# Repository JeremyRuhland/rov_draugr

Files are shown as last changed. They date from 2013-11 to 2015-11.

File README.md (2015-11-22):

Western Washington University Marine Technology Club 2014 ROV: Draugr
=====================================================================

More information can be found on my [WWU MTC page](http://goopypanther.org/seniorProjectWebsite/wwu-marine-technology-club.html) or the [main blog post](http://blog.goopypanther.org/posts/ROV_Project:_Draugr/) about Draugr.

The stuff here's pretty old and probably doesn't reflect the current state of the ROV. Some firmware tweaks may have been made last minute in responce to hardware changes. Only the basic functionality was fully implemented and tested.

You can control the ROV via a screen session and the keyboard, the actual GUI that uses the xbox controller was written by Sean and got stored elsewhere (somewhere?).

File hierarchy
--------------

 * firmware
  * C source files
 * hardware
  * Schematics and gerbers for main control board
 * protocol_documentation
  * Command protocol for designing control software

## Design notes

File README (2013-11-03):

5x h bridges
    4 input         =   20 input
                        3x 8-bit shift registers w/ spi interface
                                5 gpio: miso, mosi, sck, latch, cs
    1 output        =   5 outputs
    1 analog        =   5 analog
        
spi arm interface   =   spi interface
                        4 gpio: miso, mosi, sck, cs

conductivity sensor =   1 analog

temp sensing        =   4 analog

range finder        =   ? 
                        4 gpio

USB interface       =   1 input
                        1 interupt

-------------------------------------------------------------------------------

3 spi
2 uart for poolside comms: rx, tx
1 gpio for usb: +
1 interupt for usb: -
2 gpio for h bridge shift registers: latch, cs
5 gpio for h bridge status
5 adc for h bridge current draw
1 gpio for arm interface: cs
1 adc for water conductivity sensor
2 adc for heat pipe thermal monitors
?1 gpio for range finder: cs

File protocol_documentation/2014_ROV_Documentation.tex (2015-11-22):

\documentclass{article}
\usepackage[utf8]{inputenc}
\usepackage[english]{babel}
\usepackage{fullpage}
\usepackage[table]{xcolor}
\usepackage{graphicx}
\usepackage[parfill]{parskip}

\definecolor{lightgray}{gray}{0.9}

%\includegraphics[width=\textwidth,height=\textheight,keepaspectratio]{}
%
%\begin{figure}[!h]
%\begin{center}
%\caption{}
%\end{center}
%\end{figure}
%
%\rowcolors{1}{}{lightgray}
%\begin{tabular}{c|cc}
% &
% &
% \\
%\hline
% & & \\
% & & \\
%\end{tabular}

\title{Western Washington University Marine Technology Club\\2014 ROV Control System Documentation}
\author{Jeremy Ruhland}
\date{\today}
\begin{document}

\maketitle
\null
\pagebreak
\vspace*{\fill}
\hfill
\begin{center}
This page intentionally left blank.
\end{center}
\pagebreak

\section*{Serial Communication Protocol}
The control system uses an FTDI USB-to-TTL serial conversion chip. The host PC sends and reads commands from a virtual serial port that is automatically created upon connection to the ROV by the FTDI firmware.

Accepted commands and their behavior are described in figure \ref{fig:commandlisting}. Unlisted commands have no effect on the system. All commands are little-endian.

\begin{figure}[!h]
\begin{center}
\rowcolors{1}{}{lightgray}
\begin{tabular}{r|l|ll}
\textbf{Command} &
\textbf{Tx Value} &
\textbf{Rx Datatype} &
\textbf{Rx Description}\\
\hline
\textbf{Motor 0} Stop & ` ' (0x20) & Unsigned 16-bit & ACK (0x06) (Command sucessful) \\
Forward & `!' (0x21) & Unsigned 16-bit & ACK (0x06) (Command sucessful) \\
Backward & `''' (0x22) & Unsigned 16-bit & ACK (0x06) (Command sucessful) \\
\hline
\textbf{Motor 1} Stop & `\#' (0x23) & Unsigned 16-bit & ACK (0x06) (Command sucessful) \\
Forward & `\$' (0x24) & Unsigned 16-bit & ACK (0x06) (Command sucessful) \\
Backward & `\%' (0x25) & Unsigned 16-bit & ACK (0x06) (Command sucessful) \\
\hline
\textbf{Motor 2} Stop & `\&' (0x26) & Unsigned 16-bit & ACK (0x06) (Command sucessful) \\
Forward & `\'' (0x27) & Unsigned 16-bit & ACK (0x06) (Command sucessful) \\
Backward & `(' (0x28) & Unsigned 16-bit & ACK (0x06) (Command sucessful) \\
\hline
\textbf{Motor 3} Stop & `)' (0x29) & Unsigned 16-bit & ACK (0x06) (Command sucessful) \\
Forward & `*' (0x2A) & Unsigned 16-bit & ACK (0x06) (Command sucessful) \\
Backward & `+' (0x2B) & Unsigned 16-bit & ACK (0x06) (Command sucessful) \\
\hline
\textbf{Motor 4} Stop & ` \`' (0x2C) & Unsigned 16-bit & ACK (0x06) (Command sucessful) \\
Forward & `-' (0x2D) & Unsigned 16-bit & ACK (0x06) (Command sucessful) \\
Backward & `.' (0x2E) & Unsigned 16-bit & ACK (0x06) (Command sucessful) \\
\hline
All Motors Stop & `/' (0x2F) & Unsigned 16-bit & ACK (0x06) (Command sucessful) \\
\hline
\textbf{Toggle SW} 0 & `0' (0x30) & Unsigned 16-bit & ACK (0x06)/NAK (0x15) (Switch state on/off) \\
1 & `1' (0x31) & Unsigned 16-bit & ACK (0x06)/NAK (0x15) (Switch state on/off) \\
2 & `2' (0x32) & Unsigned 16-bit & ACK (0x06)/NAK (0x15) (Switch state on/off) \\
3 & `3' (0x33) & Unsigned 16-bit & ACK (0x06)/NAK (0x15) (Switch state on/off) \\
4 & `4' (0x34) & Unsigned 16-bit & ACK (0x06)/NAK (0x15) (Switch state on/off) \\
5 & `5' (0x35) & Unsigned 16-bit & ACK (0x06)/NAK (0x15) (Switch state on/off) \\
\hline
All Switches Off & `6' (0x36) & Unsigned 16-bit & ACK (0x06) \\
\hline
Get Motor Status & `7' (0x37) & 5x Unsigned 16-bit & ACK (0x06)/NAK (0x15) (Motor healthy/sick) \\
Get Temps & `8' (0x38) & 3x Signed 16-bit & Heat pipes 1-2 \& internal ($^\circ C$) \\
Get Motor Currents & `9' (0x39) & 5x Unsigned 16-bit & Motor 0-5 current ($mA$) \\
\hline
Get Water Conductivity & `:' (0x3A) & Unsigned 16-bit & Conductivity ($mS$) \\
Get Sonar Distance & `;' (0x3B) & Unsigned 16-bit & Distance ($CM$) \\
Get Compass Heading & `\textless' (0x3C) & Signed 16-bit & ($^\circ N$) \\

% Keeping for later & '' (0x) & Unsigned 16-bit & ACK (0x06) \\
% \textgreater == '>'
\end{tabular}
\caption{System commands and behavior}
\label{fig:commandlisting}
\end{center}
\end{figure}
\end{document}

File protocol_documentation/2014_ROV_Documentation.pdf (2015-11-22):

# Western Washington University Marine Technology Club 2014 ROV Control System Documentation

Jeremy Ruhland

February 11, 2014

1

This page intentionally left blank.

2

## Serial Communication Protocol

The control system uses an FTDI USB-to-TTL serial conversion chip. The host PC sends and reads commands from a virtual serial port that is automatically created upon connection to the ROV by the FTDI firmware.

Accepted commands and their behavior are described in figure 1. Unlisted commands have no effect on the system. All commands are little-endian.

Command | Tx Value | Rx Datatype | Rx Description
Motor 0 Stop | ‘ ’ (0x20) | Unsigned 16-bit | ACK (0x06) (Command sucessful)
Forward | ‘!’ (0x21) | Unsigned 16-bit | ACK (0x06) (Command sucessful)
Backward | ‘”’ (0x22) | Unsigned 16-bit | ACK (0x06) (Command sucessful)
Motor 1 Stop | ‘#’ (0x23) | Unsigned 16-bit | ACK (0x06) (Command sucessful)
Forward | ‘$’ (0x24) | Unsigned 16-bit | ACK (0x06) (Command sucessful)
Backward | ‘%’ (0x25) | Unsigned 16-bit | ACK (0x06) (Command sucessful)
Motor 2 Stop | ‘&’ (0x26) | Unsigned 16-bit | ACK (0x06) (Command sucessful)
Forward | ‘
| ´’ (0x27) | Unsigned 16-bit | ACK (0x06) (Command sucessful)
Backward | ‘(’ (0x28) | Unsigned 16-bit | ACK (0x06) (Command sucessful)
Motor 3 Stop | ‘)’ (0x29) | Unsigned 16-bit | ACK (0x06) (Command sucessful)
Forward | ‘*’ (0x2A) | Unsigned 16-bit | ACK (0x06) (Command sucessful)
Backward | ‘+’ (0x2B) | Unsigned 16-bit | ACK (0x06) (Command sucessful)
Motor 4 Stop | ‘
| `’ (0x2C) | Unsigned 16-bit | ACK (0x06) (Command sucessful)
Forward | ‘-’ (0x2D) | Unsigned 16-bit | ACK (0x06) (Command sucessful)
Backward | ‘.’ (0x2E) | Unsigned 16-bit | ACK (0x06) (Command sucessful)
All Motors Stop | ‘/’ (0x2F) | Unsigned 16-bit | ACK (0x06) (Command sucessful)
Toggle SW 0 | ‘0’ (0x30) | Unsigned 16-bit | ACK (0x06)/NAK (0x15) (Switch state on/off)
1 | ‘1’ (0x31) | Unsigned 16-bit | ACK (0x06)/NAK (0x15) (Switch state on/off)
2 | ‘2’ (0x32) | Unsigned 16-bit | ACK (0x06)/NAK (0x15) (Switch state on/off)
3 | ‘3’ (0x33) | Unsigned 16-bit | ACK (0x06)/NAK (0x15) (Switch state on/off)
4 | ‘4’ (0x34) | Unsigned 16-bit | ACK (0x06)/NAK (0x15) (Switch state on/off)
5 | ‘5’ (0x35) | Unsigned 16-bit | ACK (0x06)/NAK (0x15) (Switch state on/off)
All Switches Off | ‘6’ (0x36) | Unsigned 16-bit | ACK (0x06)
Get Motor Status | ‘7’ (0x37) | 5x Unsigned 16-bit | ACK (0x06)/NAK (0x15) (Motor healthy/sick)
Get Temps | ‘8’ (0x38) | 3x Signed 16-bit | Heat pipes 1-2 & internal (◦C)
Get Motor Currents | ‘9’ (0x39) | 5x Unsigned 16-bit | Motor 0-5 current (mA)
Get Water Conductivity | ‘:’ (0x3A) | Unsigned 16-bit | Conductivity (mS)
Get Sonar Distance | ‘;’ (0x3B) | Unsigned 16-bit | Distance (CM)
Get Compass Heading | ‘<’ (0x3C) | Signed 16-bit | ( ◦N)

Figure 1: System commands and behavior

3

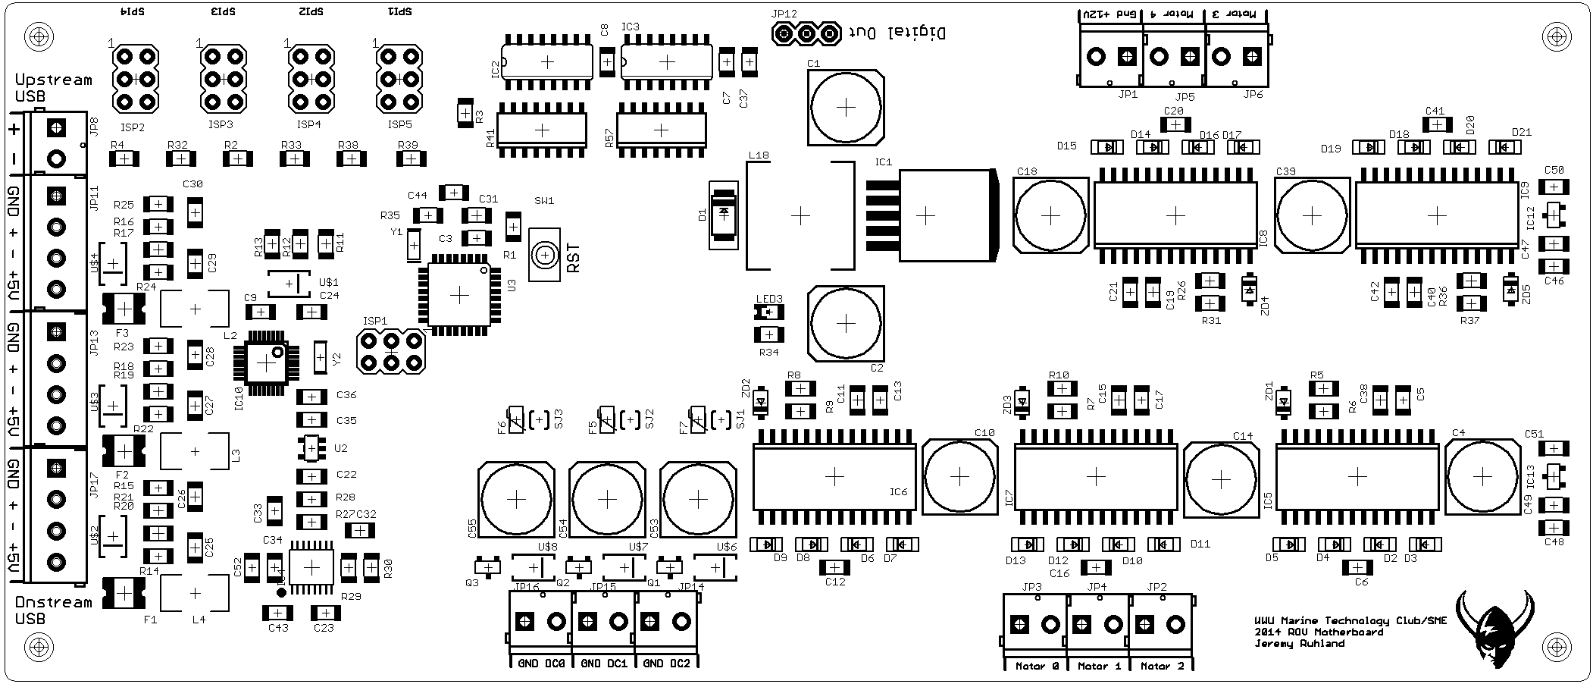
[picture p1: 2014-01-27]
hardware/motherboard_brd_bw.png

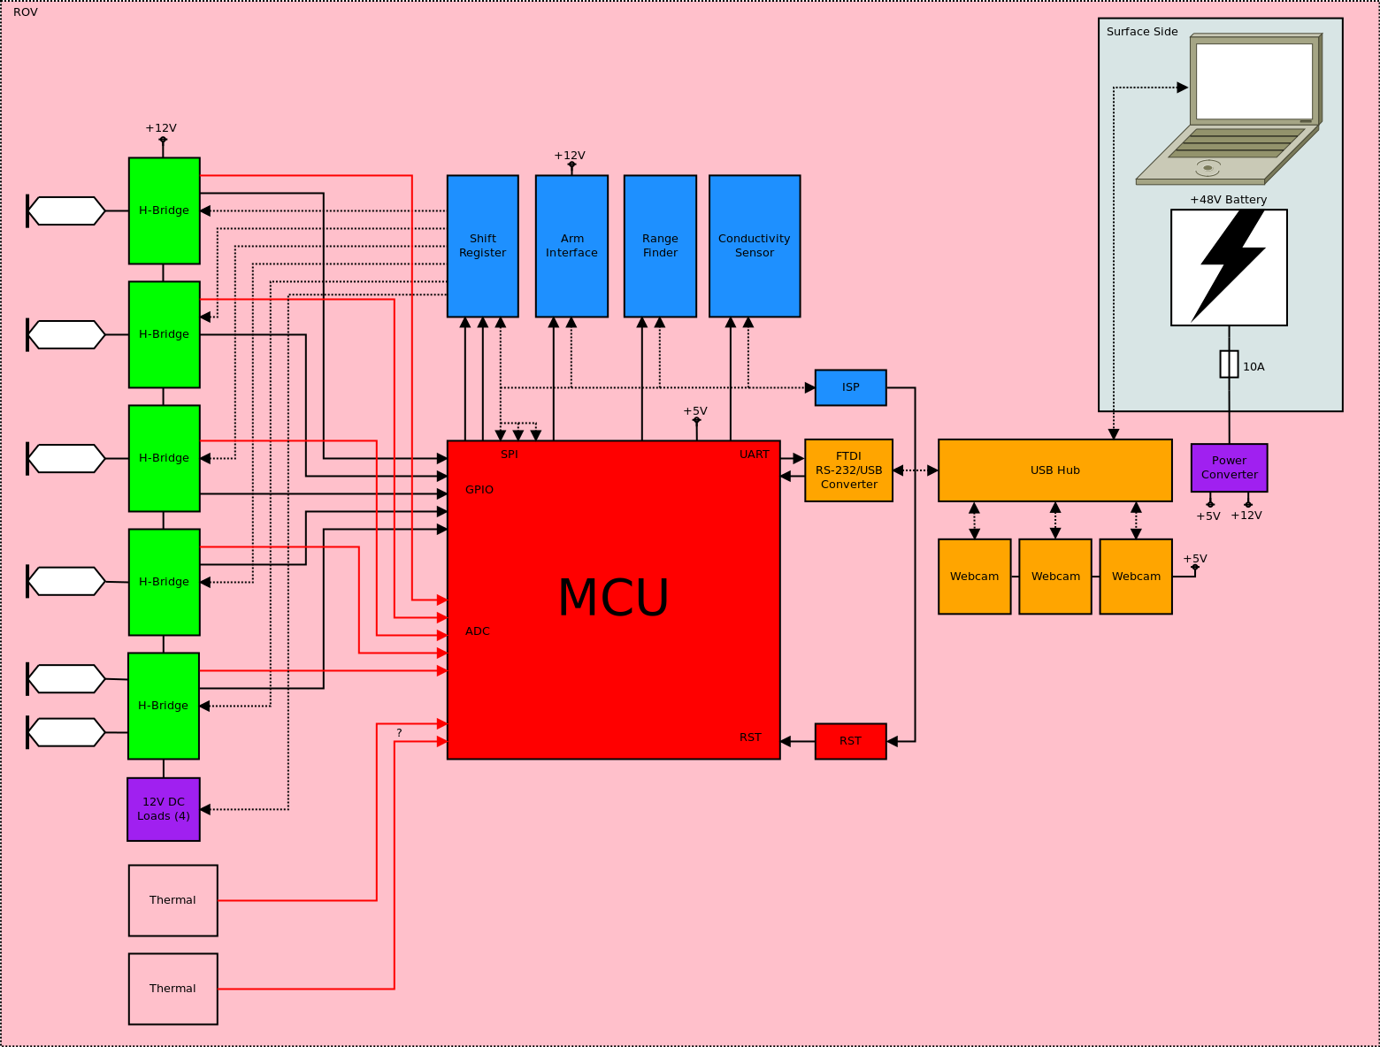
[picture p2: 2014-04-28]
hardware/architecture/System.png

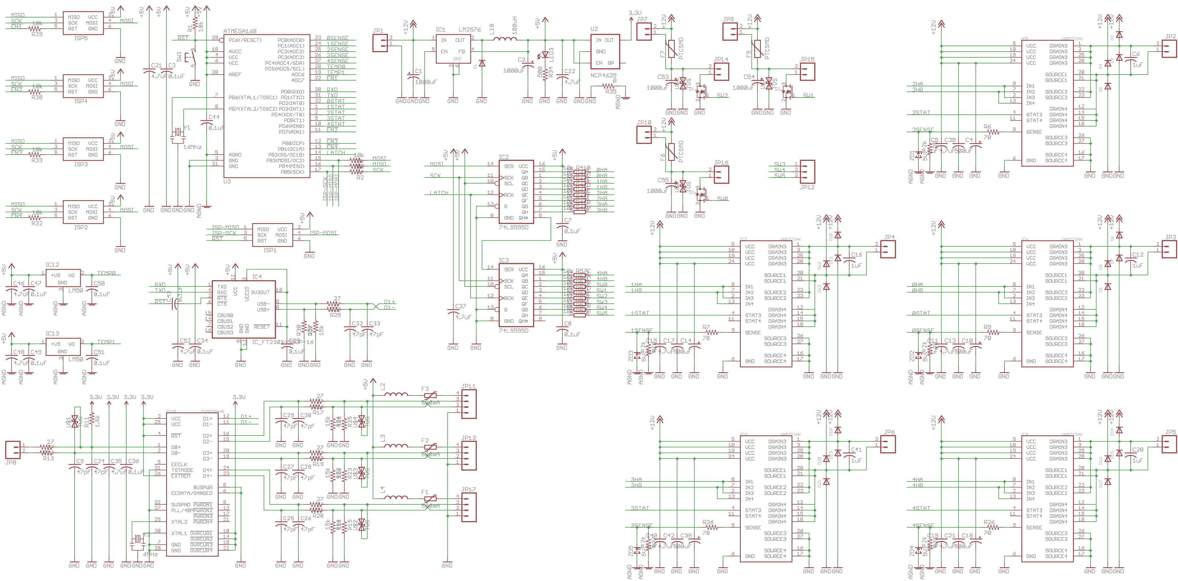
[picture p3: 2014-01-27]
hardware/motherboard_sch.png

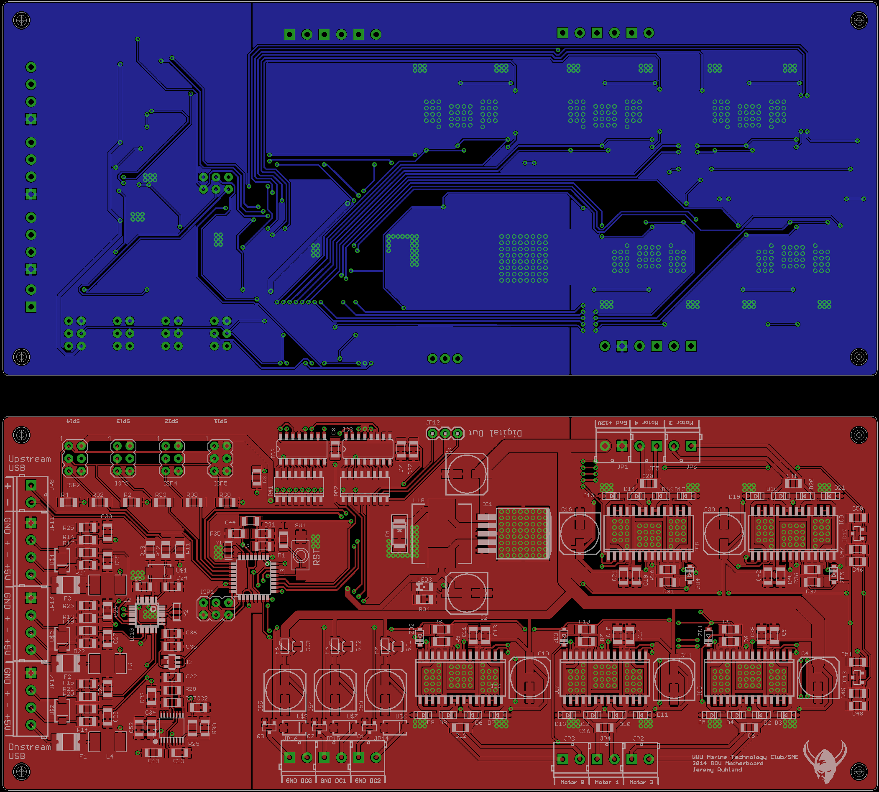
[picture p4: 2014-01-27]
hardware/motherboard_brd.png

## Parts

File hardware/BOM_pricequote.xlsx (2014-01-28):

Index | Quantity | Part Number | Description | Available Quantity | Backorder Quantity | Unit Price | Extended Price
1 | 1 | CRT1206-BY-1003ELFCT-ND (http://www.digikey.com/product-detail/en/CRT1206-BY-1003ELF/CRT1206-BY-1003ELFCT-ND/1775052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) | RES 100K OHM 1/4W .1% 1206 SMD | 1 | 0 | 0.64 | $0.64
 |  |  |  | Immediate
2 | 2 | 4816P-1-103LFCT-ND (http://www.digikey.com/product-detail/en/4816P-1-103LF/4816P-1-103LFCT-ND/3437821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) | RES ARRAY 10K OHM 8 RES 16SOIC | 2 | 0 | 0.64 | $1.28
 |  |  |  | Immediate
3 | 1 | SRR1210-101MCT-ND (http://www.digikey.com/product-detail/en/SRR1210-101M/SRR1210-101MCT-ND/2353030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) | INDUCTOR PWR 100UH 20% SHLD SMD | 1 | 0 | 0.99 | $0.99
 |  |  |  | Immediate
4 | 20 | 1276-1165-1-ND (http://www.digikey.com/product-detail/en/CL31B104JBCNNNC/1276-1165-1-ND/3889251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) | CAP CER 0.1UF 50V 5% X7R 1206 | 20 | 0 | 0.072 | $1.44
 |  |  |  | Immediate
5 | 1 | AP2125K-3.3TRG1DICT-ND (http://www.digikey.com/product-detail/en/AP2125K-3.3TRG1/AP2125K-3.3TRG1DICT-ND/4505268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) | IC REG LDO 3.3V 0.3A SOT25 | 1 | 0 | 0.53 | $0.53
 |  |  |  | Immediate
6 | 1 | ATMEGA328-AU-ND (http://www.digikey.com/product-detail/en/ATMEGA328-AU/ATMEGA328-AU-ND/2271029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) | IC MCU 8BIT 32KB FLASH 32TQFP | 1 | 0 | 2.84 | $2.84
 |  |  |  | Immediate
7 | 13 | 493-2193-1-ND (http://www.digikey.com/product-detail/en/UWT1E331MNL1GS/493-2193-1-ND/590168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) | CAP ALUM 330UF 25V 20% SMD | 13 | 0 | 0.566 | $7.36
 |  |  |  | Immediate
8 | 10 | 311-1158-1-ND (http://www.digikey.com/product-detail/en/CC1206JRNPO9BN470/311-1158-1-ND/303068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) | CAP CER 47PF 50V 5% NPO 1206 | 10 | 0 | 0.107 | $1.07
 |  |  |  | Immediate
9 | 5 | 478-5329-1-ND (http://www.digikey.com/product-detail/en/12063C105JAT2A/478-5329-1-ND/1950996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) | CAP CER 1UF 25V 5% X7R 1206 | 5 | 0 | 0.81 | $4.05
 |  |  |  | Immediate
10 | 1 | 535-9367-1-ND (http://www.digikey.com/product-detail/en/AWSCR-6.00MGD-T/535-9367-1-ND/675779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) | RESONATOR CER 6.00MHZ W/CAP SMD | 1 | 0 | 0.38 | $0.38
 |  |  |  | Immediate
11 | 1 | 493-6279-1-ND (http://www.digikey.com/product-detail/en/UUX2A100MNL1GS/493-6279-1-ND/3438792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) | CAP ALUM 10UF 100V 20% SMD | 1 | 0 | 0.63 | $0.63
 |  |  |  | Immediate
12 | 1 | RMCF1206FT100KCT-ND (http://www.digikey.com/product-detail/en/RMCF1206FT100K/RMCF1206FT100KCT-ND/1942730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) | RES 100K OHM 1/4W 1% 1206 | 1 | 0 | 0.06 | $0.06
 |  |  |  | Immediate
13 | 5 | RMCF1206FT68R0CT-ND (http://www.digikey.com/product-detail/en/RMCF1206FT68R0/RMCF1206FT68R0CT-ND/2418813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) | RES 68 OHM 1/4W 1% 1206 | 5 | 0 | 0.06 | $0.30
 |  |  |  | Immediate
14 | 10 | RMCF1206FT27R0CT-ND (http://www.digikey.com/product-detail/en/RMCF1206FT27R0/RMCF1206FT27R0CT-ND/2418671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) | RES 27 OHM 1/4W 1% 1206 | 10 | 0 | 0.044 | $0.44
 |  |  |  | Immediate
15 | 1 | RMCF1206FT1K50CT-ND (http://www.digikey.com/product-detail/en/RMCF1206FT1K50/RMCF1206FT1K50CT-ND/1942679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) | RES 1.5K OHM 1/4W 1% 1206 | 1 | 0 | 0.06 | $0.06
 |  |  |  | Immediate
16 | 1 | 535-10008-1-ND (http://www.digikey.com/product-detail/en/AWSCR-16.00CV-T/535-10008-1-ND/2001631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) | RESONATOR CER 16.00MHZ W/CAP SMD | 1 | 0 | 0.38 | $0.38
 |  |  |  | Immediate
17 | 1 | RMCF1206FT560RCT-ND (http://www.digikey.com/product-detail/en/RMCF1206FT560R/RMCF1206FT560RCT-ND/2418781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) | RES 560 OHM 1/4W 1% 1206 | 1 | 0 | 0.06 | $0.06
 |  |  |  | Immediate
18 | 11 | RMCF1206FT10K0CT-ND (http://www.digikey.com/product-detail/en/RMCF1206FT10K0/RMCF1206FT10K0CT-ND/1942707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) | RES 10K OHM 1/4W 1% 1206 | 11 | 0 | 0.044 | $0.48
 |  |  |  | Immediate
19 | 8 | RMCF1206FT15K0CT-ND (http://www.digikey.com/product-detail/en/RMCF1206FT15K0/RMCF1206FT15K0CT-ND/1942710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) | RES 15K OHM 1/4W 1% 1206 | 8 | 0 | 0.06 | $0.48
 |  |  |  | Immediate
20 | 1 | 475-1416-1-ND (http://www.digikey.com/product-detail/en/LH+N974-KN-1/475-1416-1-ND/1802603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) | LED CHIPLED 645NM RED DIFF 1206 | 1 | 0 | 0.11 | $0.11
 |  |  |  | Immediate
21 | 2 | ED2740-ND (http://www.digikey.com/product-detail/en/OSTTE020104/ED2740-ND/2351816?itemSeq=143388415&uq=635265099481864606) | TERMINAL BLOCK 3.5MM 2POS PCB | 2 | 0 | 0.36 | $0.72
 |  |  |  | Immediate
22 | 5 | RMCF1206FT2K00CT-ND (http://www.digikey.com/product-detail/en/RMCF1206FT2K00/RMCF1206FT2K00CT-ND/1942681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) | RES 2K OHM 1/4W 1% 1206 | 5 | 0 | 0.06 | $0.30
 |  |  |  | Immediate
23 | 5 | 609-2845-ND (http://www.digikey.com/product-detail/en/75869-131LF/609-2845-ND/1302569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) | CONN HEADER 6POS DUAL VERT PCB | 5 | 0 | 0.74 | $3.70
 |  |  |  | Immediate
24 | 5 | 568-6370-1-ND (http://www.digikey.com/product-detail/en/NZH5V1B%2c115/568-6370-1-ND/2531657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) | DIODE ZENER 5.1V 500MW SOD123F | 5 | 0 | 0.21 | $1.05
 |  |  |  | Immediate
25 | 1 | 768-1135-1-ND (http://www.digikey.com/product-detail/en/FT230XS-R/768-1135-1-ND/3029155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) | IC USB SERIAL BASIC UART 16SSOP | 1 | 0 | 2.38 | $2.38
 |  |  |  | Immediate
26 | 1 | S1D-FDICT-ND (http://www.digikey.com/product-detail/en/S1D-13-F/S1D-FDICT-ND/815934?itemSeq=143388420&uq=635265099481864606) | DIODE GEN PURPOSE 200V 1A SMA | 1 | 0 | 0.1 | $0.10
 |  |  |  | Immediate
27 | 6 | ED2744-ND (http://www.digikey.com/product-detail/en/OSTTE060104/ED2744-ND/2351820?itemSeq=143388421&uq=635265099481864606) | TERMINAL BLOCK 3.5MM 6POS PCB | 6 | 0 | 0.85 | $5.10
 |  |  |  | Immediate
28 | 1 | LM2576D2TR4-5GOSCT-ND (http://www.digikey.com/product-detail/en/LM2576D2TR4-5G/LM2576D2TR4-5GOSCT-ND/2120633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) | IC REG BUCK 5V 3A D2PAK | 1 | 0 | 2.51 | $2.51
 |  |  |  | Immediate
29 | 1 | P13597SCT-ND (http://www.digikey.com/product-detail/en/EVQ-PNF04M/P13597SCT-ND/1245518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) | SWITCH TACTILE SPST-NO 0.05A 12V | 1 | 0 | 0.72 | $0.72
 |  |  |  | Immediate
30 | 2 | LM50CIM3X/NOPBCT-ND (http://www.digikey.com/product-detail/en/LM50CIM3X%2fNOPB/LM50CIM3X%2fNOPBCT-ND/3440178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) | IC SENSOR TEMPERATURE SOT23-3 | 2 | 0 | 0.99 | $1.98
 |  |  |  | Immediate
31 | 13 | 399-8203-1-ND (http://www.digikey.com/product-detail/en/C1206C475J3RACTU/399-8203-1-ND/3471926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) | CAP CER 4.7UF 25V 5% X7R 1206 | 13 | 0 | 1.058 | $13.75
 |  |  |  | Immediate
32 | 7 | IRFML8244TRPBFCT-ND (http://www.digikey.com/product-detail/en/IRFML8244TRPBF/IRFML8244TRPBFCT-ND/2538166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) | MOSFET N-CH 25V 5.8A SOT23 | 7 | 0 | 0.38 | $2.66
 |  |  |  | Immediate
33 | 3 | 490-6706-1-ND (http://www.digikey.com/product-detail/en/LQM31PN4R7M00L/490-6706-1-ND/3845903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) | INDUCTOR 4.7UH 20% 1206 | 3 | 0 | 0.38 | $1.14
 |  |  |  | Immediate
34 | 1 | MCP3001T-I/SNCT-ND (http://www.digikey.com/product-detail/en/MCP3001T-I%2fSN/MCP3001T-I%2fSNCT-ND/669495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) | IC ADC 10BIT 2.7V 1CH SPI 8-SOIC | 1 | 0 | 1.99 | $1.99
 |  |  |  | Immediate
35 | 2 | 296-14857-1-ND (http://www.digikey.com/product-detail/en/SN74HC595DR/296-14857-1-ND/562567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) | IC 8BIT SHIFT REG 3ST-OUT 16SOIC | 2 | 0 | 0.59 | $1.18
 |  |  |  | Immediate
36 | 4 | 507-1762-1-ND (http://www.digikey.com/product-detail/en/0ZCG0050AF2C/507-1762-1-ND/4156148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) | PTC RESETTBLE 0.50A 30V CHIP 181 | 4 | 0 | 0.12 | $0.48
 |  |  |  | Immediate
37 | 3 | 507-1084-1-ND (http://www.digikey.com/product-detail/en/C1Q+4/507-1084-1-ND/615045?itemSeq=143388431&uq=635265099481864606) | FUSE 4A 125V 1206 FAST C1Q | 3 | 0 | 0.31 | $0.93
 |  |  |  | Immediate
38 | 8 | SMAJ51CABCT-ND (http://www.digikey.com/product-detail/en/SMAJ51CA/SMAJ51CABCT-ND/2253548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) | TVS DIODE 51VWM SMD | 8 | 0 | 0.44 | $3.52
 |  |  |  | Immediate
39 | 5 | 497-11677-1-ND (http://www.digikey.com/product-detail/en/VN5772AKTR-E/497-11677-1-ND/2746906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) | IC MOTOR DRIVER PAR 28SO | 5 | 0 | 5.29 | $26.45
 |  |  |  | Immediate
40 | 1 | 296-27131-1-ND (http://www.digikey.com/product-detail/en/TUSB2046BVFR/296-27131-1-ND/2255387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) | IC 4-PORT USB HUB 32-LQFP | 1 | 0 | 3.46 | $3.46
 |  |  |  | Immediate
41 | 1 | BSS84CT-ND (http://www.digikey.com/product-detail/en/BSS84/BSS84CT-ND/244297?itemSeq=143388435&uq=635265099481864606) | MOSFET P-CH 50V 130MA SOT-23 | 1 | 0 | 0.22 | $0.22
 |  |  |  | Immediate
42 | 20 | 568-6749-1-ND (http://www.digikey.com/product-detail/en/PMEG4030ER%2c115/568-6749-1-ND/2676789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) | DIODE SCHOTTKY 40V 3A SOD123W | 20 | 0 | 0.371 | $7.42
 |  |  |  | Immediate
 |  |  |  |  |  | Subtotal | $105.34
 |  |  |  |  |  | Shipping | $5.66
 |  |  |  |  |  | Sales Tax (https://www.digikey.com/classic/Help.aspx?id=Sales%20Tax%20Help) | unknown
 |  |  |  |  |  | Total | unknown

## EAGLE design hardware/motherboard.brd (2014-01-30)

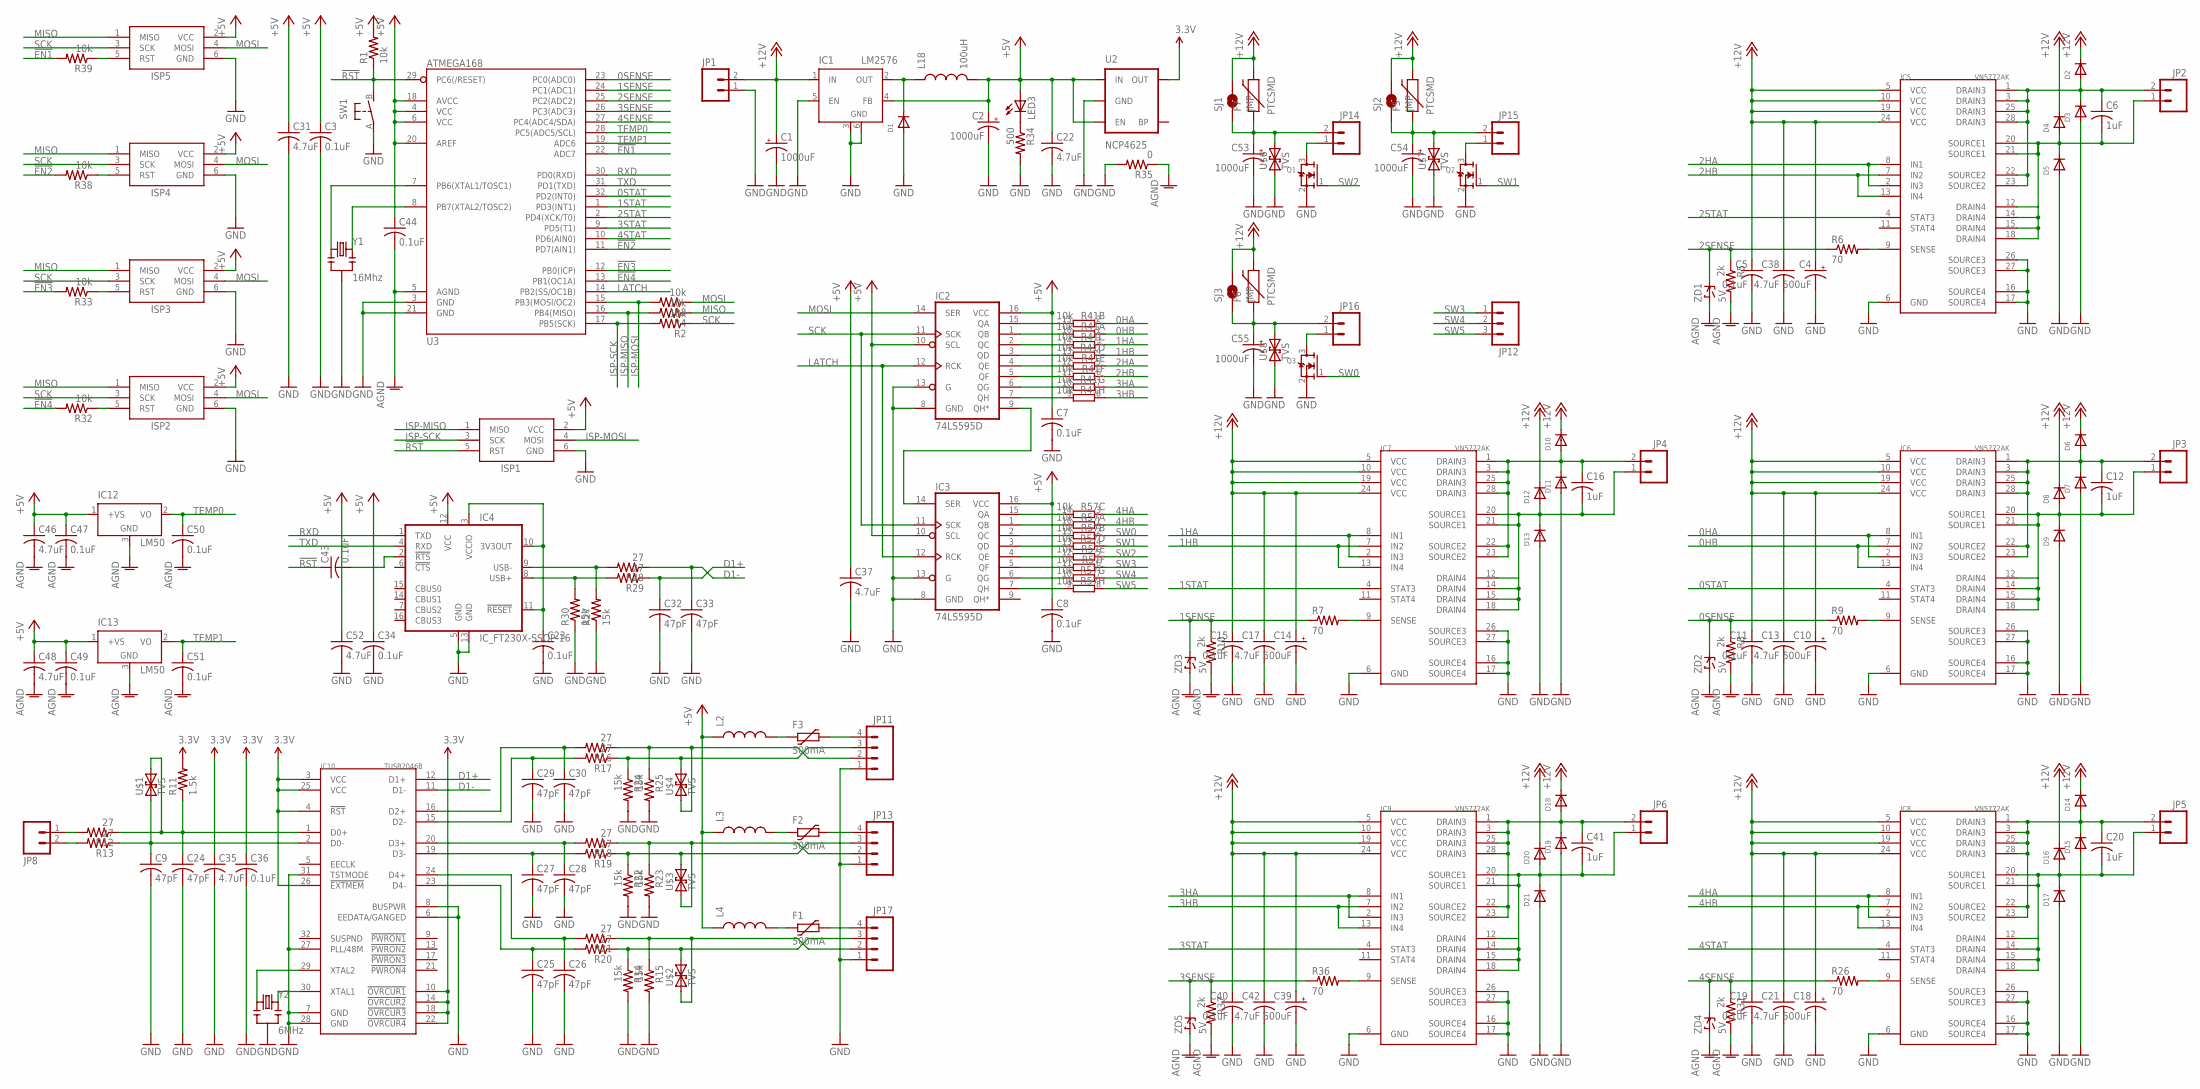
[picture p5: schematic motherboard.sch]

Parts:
C1, C2, C53, C54, C55: 1000uF; 153CLV-0807
C3, C5, C7, C8, C11, C15, C19, C23, C34, C36, C40, C43, C44, C47, C49, C50, C51: 0.1uF; C1206
C4, C10, C14, C18, C39: 500uF; 153CLV-0807
C6, C12, C16, C20, C41: 1uF; C1206
C9, C24, C25, C26, C27, C28, C29, C30, C32, C33: 47pF; C1206
C13, C17, C21, C22, C31, C35, C37, C38, C42, C46, C48, C52: 4.7uF; C1206
D1: DIODESMA; SMADIODE
D2, D3, D4, D5, D6, D7, D8, D9, D10, D11, D12, D13, D14, D15, D16, D17, D18, D19, D20, D21: DIODESOD-123; SOD-123
F1, F2, F3: 500mA; PTC1812L
F5, F6, F7: PTCSMD; PTC-1206
IC1: LM2576; TO263-5
IC2, IC3: 74LS595D; SO16
IC4: IC_FT230X-SSOP-16; SSOP-16-FTDI
IC5, IC6, IC7, IC8, IC9: VN5772AK; SO-28
IC10: TUSB2046B; LQFP-32
IC12, IC13: LM50; SOT23
ISP1, ISP2, ISP3, ISP4, ISP5: AVRISP-6; AVRISP
JP1, JP2, JP3, JP4, JP5, JP6, JP8, JP14, JP15, JP16: M023.5MM; SCREWTERMINAL-3.5MM-2
JP11, JP13, JP17: M04SCREW; SCREWTERMINAL-3.5MM-4
JP12: M03PTH; 1X03
L2, L3, L4: INDUCTOR1206H*; INDUCTOR-1206
L18: 100uH; CDRH125
LED3: LEDCHIPLED_1206; CHIPLED_1206
Q1, Q2, Q3: MOSFET-NREFLOW; SOT23
R1, R2, R3, R4, R32, R33, R38, R39: 10k; R1206
R5, R8, R10, R31, R37: 2k; R1206
R6, R7, R9, R26, R36: 70; R1206
R11: 1.5k; R1206
R12, R13, R16, R17, R18, R19, R20, R21, R28, R29: 27; R1206
R14, R15, R22, R23, R24, R25, R27, R30: 15k; R1206
R34: 500; R1206
R35: 0; R1206
R41, R57: 10k; SO16
SJ1, SJ2, SJ3: JMP; SJ_2S-NO
SW1: FSMSM
U2: NCP4625; SOT23-5
U3: ATMEGA168; TQFP32-08
U$1, U$2, U$3, U$4, U$6, U$7, U$8: TVS; SMA-DIODE
Y1: 16Mhz; RESONATOR-SMD
Y2: 6MHz; RESONATOR-SMD
ZD1, ZD2, ZD3, ZD4, ZD5: 5V; SOD-123

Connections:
0HA: IC6.2 (IN3), IC6.8 (IN1), R41.2 (1)
0HB: IC6.7 (IN2), IC6.13 (IN4), R41.1
0SENSE: R8.1, R9.1, U3.23 (PC0(ADC0)), ZD2.C
0STAT: IC6.4 (STAT3), U3.32 (PD2(INT0))
1HA: IC7.2 (IN3), IC7.8 (IN1), R41.3 (1)
1HB: IC7.7 (IN2), IC7.13 (IN4), R41.4 (1)
1SENSE: R7.1, R10.1, U3.24 (PC1(ADC1)), ZD3.C
1STAT: IC7.4 (STAT3), U3.1 (PD3(INT1))
2HA: IC5.2 (IN3), IC5.8 (IN1), R41.5 (1)
2HB: IC5.7 (IN2), IC5.13 (IN4), R41.6 (1)
2SENSE: R5.1, R6.1, U3.25 (PC2(ADC2)), ZD1.C
2STAT: IC5.4 (STAT3), U3.2 (PD4(XCK/T0))
3.3V: C35.1, C36.1, IC10.3 (VCC), IC10.4 (!RST), IC10.10 (!OVRCUR1), IC10.14 (!OVRCUR2), IC10.18 (!OVRCUR3), IC10.22 (!OVRCUR4), IC10.25 (VCC), IC10.26 (!EXTMEM), R11.2, U2.5 (OUT)
3HA: IC9.2 (IN3), IC9.8 (IN1), R41.7 (1)
3HB: IC9.7 (IN2), IC9.13 (IN4), R41.8 (1)
3SENSE: R36.1, R37.1, U3.26 (PC3(ADC3)), ZD5.C
3STAT: IC9.4 (STAT3), U3.9 (PD5(T1))
4HA: IC8.2 (IN3), IC8.8 (IN1), R57.3 (1)
4HB: IC8.7 (IN2), IC8.13 (IN4), R57.1
4SENSE: R26.1, R31.1, U3.27 (PC4(ADC4/SDA)), ZD4.C
4STAT: IC8.4 (STAT3), U3.10 (PD6(AIN0))
!EN1: R39.2, U3.22 (ADC7)
!EN2: R38.2, U3.11 (PD7(AIN1))
!EN3: R33.2, U3.12 (PB0(ICP))
!EN4: R32.2, U3.13 (PB1(OC1A))
!RST: C43.1, ISP1.5 (RST), R1.1, SW1.B (S), U3.29 (PC6(/RESET))
+5V: C2.+, C3.1, C7.1, C8.1, C22.1, C31.1, C34.1, C37.1, C44.1, C46.1, C47.1, C48.1, C49.1, C52.1, IC1.4 (FB), IC2.10 (SCL), IC2.16 (VCC), IC3.10 (SCL), IC3.16 (VCC), IC4.12 (VCC), IC12.1 (+VS), IC13.1 (+VS), ISP1.2 (VCC), ISP2.2 (VCC), ISP3.2 (VCC), ISP4.2 (VCC), ISP5.2 (VCC), L2.P$1 (1), L3.P$1 (1), L4.P$1 (1), L18.2, LED3.A, R1.2, U2.1 (IN), U2.3 (EN), U3.4 (VCC), U3.6 (VCC), U3.18 (AVCC), U3.20 (AREF)
+12V: C1.+, C4.+, C5.1, C10.+, C11.1, C13.1, C14.+, C15.1, C17.1, C18.+, C19.1, C21.1, C38.1, C39.+, C40.1, C42.1, D2.C, D4.C, D6.C, D8.C, D10.C, D12.C, D14.C, D16.C, D18.C, D20.C, F5.2, F6.2, F7.2, IC1.1 (IN), IC5.5 (VCC), IC5.10 (VCC), IC5.19 (VCC), IC5.24 (VCC), IC6.5 (VCC), IC6.10 (VCC), IC6.19 (VCC), IC6.24 (VCC), IC7.5 (VCC), IC7.10 (VCC), IC7.19 (VCC), IC7.24 (VCC), IC8.5 (VCC), IC8.10 (VCC), IC8.19 (VCC), IC8.24 (VCC), IC9.5 (VCC), IC9.10 (VCC), IC9.19 (VCC), IC9.24 (VCC), JP1.2, SJ1.2, SJ2.2, SJ3.2
AGND: C44.2, C46.2, C47.2, C48.2, C49.2, C50.2, C51.2, IC12.3 (GND), IC13.3 (GND), R5.2, R8.2, R10.2, R31.2, R35.1, R37.2, U3.5 (AGND), ZD1.A, ZD2.A, ZD3.A, ZD4.A, ZD5.A
D1+: C32.1, IC10.12 (D1+), R29.1
D1-: C33.1, IC10.11 (D1-), R28.1
GND: C1.-, C2.-, C3.2, C4.-, C5.2, C7.2, C8.2, C9.2, C10.-, C11.2, C13.2, C14.-, C15.2, C17.2, C18.-, C19.2, C21.2, C22.2, C23.2, C24.2, C25.2, C26.2, C27.2, C28.2, C29.2, C30.2, C31.2, C32.2, C33.2, C34.2, C35.2, C36.2, C37.2, C38.2, C39.-, C40.2, C42.2, C52.2, C53.-, C54.-, C55.-, D1.A, D3.A, D5.A, D7.A, D9.A, D11.A, D13.A, D15.A, D17.A, D19.A, D21.A, IC1.3 (GND), IC1.5 (EN), IC1.6 (GND), IC2.8 (GND), IC2.13 (G), IC3.8 (GND), IC3.13 (G), IC4.5 (GND), IC4.13 (GND), IC5.6 (GND), IC5.16 (SOURCE4), IC5.17 (SOURCE4), IC5.26 (SOURCE3), IC5.27 (SOURCE3), IC6.6 (GND), IC6.16 (SOURCE4), IC6.17 (SOURCE4), IC6.26 (SOURCE3), IC6.27 (SOURCE3), IC7.6 (GND), IC7.16 (SOURCE4), IC7.17 (SOURCE4), IC7.26 (SOURCE3), IC7.27 (SOURCE3), IC8.6 (GND), IC8.16 (SOURCE4), IC8.17 (SOURCE4), IC8.26 (SOURCE3), IC8.27 (SOURCE3), IC9.6 (GND), IC9.16 (SOURCE4), IC9.17 (SOURCE4), IC9.26 (SOURCE3), IC9.27 (SOURCE3), IC10.6 (EEDATA/GANGED), IC10.7 (GND), IC10.8 (BUSPWR), IC10.27 (PLL/48M), IC10.28 (GND), IC10.31 (TSTMODE), ISP1.6 (GND), ISP2.6 (GND), ISP3.6 (GND), ISP4.6 (GND), ISP5.6 (GND), JP1.1, JP11.1, JP13.1, JP17.1, Q1.2 (S), Q2.2 (S), Q3.2 (S), R14.2, R15.2, R22.2, R23.2, R24.2, R25.2, R27.1, R30.1, R34.2, R35.2, SW1.A, U2.2 (GND), U3.3 (GND), U3.21 (GND), U$6.A (1), U$7.A (1), U$8.A (1), Y1.2, Y2.2
ISP-MISO: ISP1.1 (MISO), R4.2, U3.16 (PB4(MISO))
ISP-MOSI: ISP1.4 (MOSI), R3.2, U3.15 (PB3(MOSI/OC2))
ISP-SCK: ISP1.3 (SCK), R2.2, U3.17 (PB5(SCK))
LATCH: IC2.12 (RCK), IC3.12 (RCK), U3.14 (PB2(SS/OC1B))
MISO: ISP2.1 (MISO), ISP3.1 (MISO), ISP4.1 (MISO), ISP5.1 (MISO), R4.1
MOSI: IC2.14 (SER), ISP2.4 (MOSI), ISP3.4 (MOSI), ISP4.4 (MOSI), ISP5.4 (MOSI), R3.1
unnamed: D1.C, IC1.2 (OUT), L18.1
unnamed: U3.8 (PB7(XTAL2/TOSC2)), Y1.3
unnamed: C12.2, D8.A, D9.C, IC6.12 (DRAIN4), IC6.14 (DRAIN4), IC6.15 (DRAIN4), IC6.18 (DRAIN4), IC6.20 (SOURCE1), IC6.21 (SOURCE1), JP3.1
unnamed: U3.7 (PB6(XTAL1/TOSC1)), Y1.1
unnamed: C12.1, D6.A, D7.C, IC6.1 (DRAIN3), IC6.3 (DRAIN3), IC6.22 (SOURCE2), IC6.23 (SOURCE2), IC6.25 (DRAIN3), IC6.28 (DRAIN3), JP3.2
unnamed: IC2.9 (QH*), IC3.14 (SER)
unnamed: C9.1, IC10.2 (D0-), R13.1, U$1.A (1)
unnamed: C16.2, D12.A, D13.C, IC7.12 (DRAIN4), IC7.14 (DRAIN4), IC7.15 (DRAIN4), IC7.18 (DRAIN4), IC7.20 (SOURCE1), IC7.21 (SOURCE1), JP4.1
unnamed: C16.1, D10.A, D11.C, IC7.1 (DRAIN3), IC7.3 (DRAIN3), IC7.22 (SOURCE2), IC7.23 (SOURCE2), IC7.25 (DRAIN3), IC7.28 (DRAIN3), JP4.2
unnamed: C20.2, D16.A, D17.C, IC8.12 (DRAIN4), IC8.14 (DRAIN4), IC8.15 (DRAIN4), IC8.18 (DRAIN4), IC8.20 (SOURCE1), IC8.21 (SOURCE1), JP5.1
unnamed: C20.1, D14.A, D15.C, IC8.1 (DRAIN3), IC8.3 (DRAIN3), IC8.22 (SOURCE2), IC8.23 (SOURCE2), IC8.25 (DRAIN3), IC8.28 (DRAIN3), JP5.2
unnamed: C41.2, D20.A, D21.C, IC9.12 (DRAIN4), IC9.14 (DRAIN4), IC9.15 (DRAIN4), IC9.18 (DRAIN4), IC9.20 (SOURCE1), IC9.21 (SOURCE1), JP6.1
unnamed: C6.2, D4.A, D5.C, IC5.12 (DRAIN4), IC5.14 (DRAIN4), IC5.15 (DRAIN4), IC5.18 (DRAIN4), IC5.20 (SOURCE1), IC5.21 (SOURCE1), JP2.1
unnamed: C41.1, D18.A, D19.C, IC9.1 (DRAIN3), IC9.3 (DRAIN3), IC9.22 (SOURCE2), IC9.23 (SOURCE2), IC9.25 (DRAIN3), IC9.28 (DRAIN3), JP6.2
unnamed: IC3.7 (QH), R57.9 (2)
unnamed: C43.2, IC4.2 (!RTS)
unnamed: IC3.6 (QG), R57.10 (2)
unnamed: IC3.5 (QF), R57.11 (2)
unnamed: C24.1, IC10.1 (D0+), R11.1, R12.1, U$1.C (2)
unnamed: JP17.2, R15.1, R21.1, U$2.A (1)
unnamed: IC10.30 (XTAL1), Y2.3
unnamed: IC10.29 (XTAL2), Y2.1
unnamed: JP17.3, R14.1, R20.1, U$2.C (2)
unnamed: JP13.3, R19.1, R22.1, U$3.C (2)
unnamed: C30.1, IC10.16 (D2+), R16.2
unnamed: C29.1, IC10.15 (D2-), R17.2
unnamed: C28.1, IC10.20 (D3+), R18.2
unnamed: C27.1, IC10.19 (D3-), R19.2
unnamed: C25.1, IC10.23 (D4-), R20.2
unnamed: C26.1, IC10.24 (D4+), R21.2
unnamed: JP13.2, R18.1, R23.1, U$3.A (1)
unnamed: JP11.3, R17.1, R24.1, U$4.C (2)
unnamed: JP11.2, R16.1, R25.1, U$4.A (1)
unnamed: F1.2, JP17.4
unnamed: F2.2, JP13.4
unnamed: F3.2, JP11.4
unnamed: C23.1, IC4.3 (VCCIO), IC4.10 (3V3OUT), IC4.11 (!RESET)
unnamed: IC4.9 (USB-), R27.2, R28.2
unnamed: IC4.8 (USB+), R29.2, R30.2
unnamed: F3.1, L2.P$2 (2)
unnamed: F2.1, L3.P$2 (2)
unnamed: JP14.1, Q1.3 (D)
unnamed: JP8.1, R12.2
unnamed: JP8.2, R13.2
unnamed: LED3.C, R34.1
unnamed: JP15.1, Q2.3 (D)
unnamed: JP16.1, Q3.3 (D)
unnamed: F1.1, L4.P$2 (2)
unnamed: C55.+, F6.1, JP16.2, SJ3.1, U$8.C (2)
unnamed: ISP2.5 (RST), R32.1
unnamed: ISP3.5 (RST), R33.1
unnamed: ISP4.5 (RST), R38.1
unnamed: C54.+, F5.1, JP15.2, SJ2.1, U$7.C (2)
unnamed: C53.+, F7.1, JP14.2, SJ1.1, U$6.C (2)
unnamed: IC3.4 (QE), R57.12 (2)
unnamed: ISP5.5 (RST), R39.1
unnamed: C6.1, D2.A, D3.C, IC5.1 (DRAIN3), IC5.3 (DRAIN3), IC5.22 (SOURCE2), IC5.23 (SOURCE2), IC5.25 (DRAIN3), IC5.28 (DRAIN3), JP2.2
unnamed: IC3.3 (QD), R57.13 (2)
unnamed: IC3.2 (QC), R57.15 (2)
unnamed: IC3.1 (QB), R57.16 (2)
unnamed: IC3.15 (QA), R57.14 (2)
unnamed: IC2.7 (QH), R41.9 (2)
unnamed: IC2.6 (QG), R41.10 (2)
unnamed: IC2.5 (QF), R41.11 (2)
unnamed: IC2.4 (QE), R41.12 (2)
unnamed: IC2.3 (QD), R41.13 (2)
unnamed: IC2.2 (QC), R41.14 (2)
unnamed: IC2.1 (QB), R41.16 (2)
unnamed: IC2.15 (QA), R41.15 (2)
unnamed: IC5.9 (SENSE), R6.2
unnamed: IC7.9 (SENSE), R7.2
unnamed: IC6.9 (SENSE), R9.2
unnamed: IC9.9 (SENSE), R36.2
unnamed: IC8.9 (SENSE), R26.2
RXD: IC4.1 (TXD), U3.30 (PD0(RXD))
SCK: IC2.11 (SCK), IC3.11 (SCK), ISP2.3 (SCK), ISP3.3 (SCK), ISP4.3 (SCK), ISP5.3 (SCK), R2.1
SW0: Q3.1 (G), R57.2 (1)
SW1: Q2.1 (G), R57.4 (1)
SW2: Q1.1 (G), R57.5 (1)
SW3: JP12.1, R57.6 (1)
SW4: JP12.2, R57.7 (1)
SW5: JP12.3, R57.8 (1)
TEMP0: C50.1, IC12.2 (VO), U3.28 (PC5(ADC5/SCL))
TEMP1: C51.1, IC13.2 (VO), U3.19 (ADC6)
TXD: IC4.4 (RXD), U3.31 (PD1(TXD))

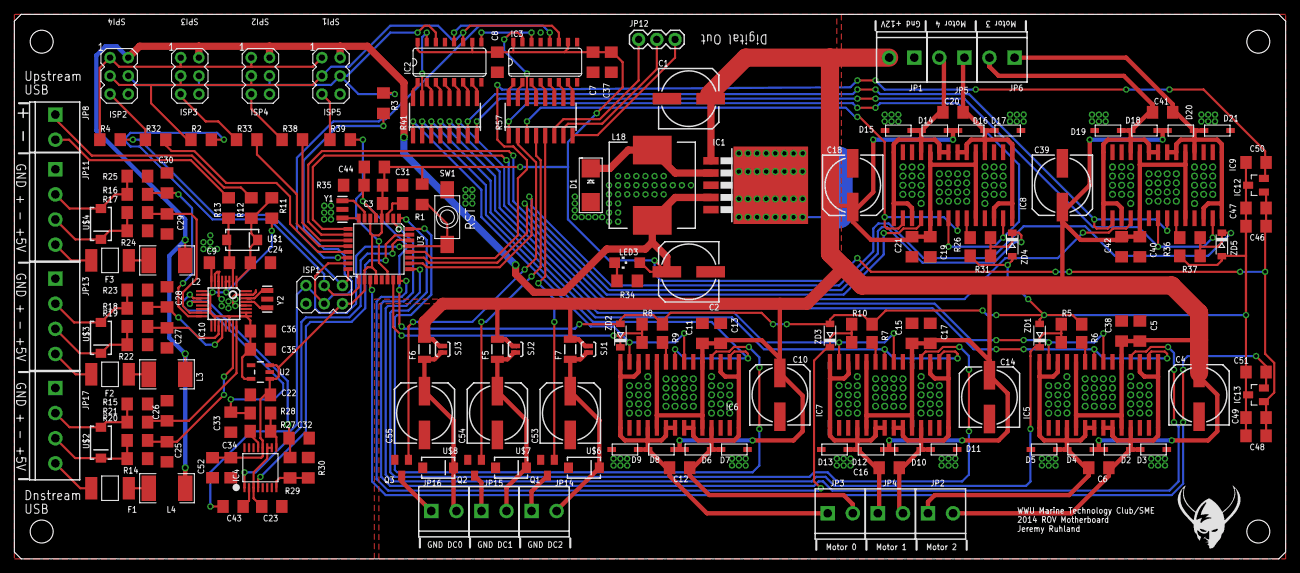
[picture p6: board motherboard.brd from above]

Board: 2 copper layers, 177.2 x 75.9 mm, 181 parts (0 on the bottom side), 123 nets.

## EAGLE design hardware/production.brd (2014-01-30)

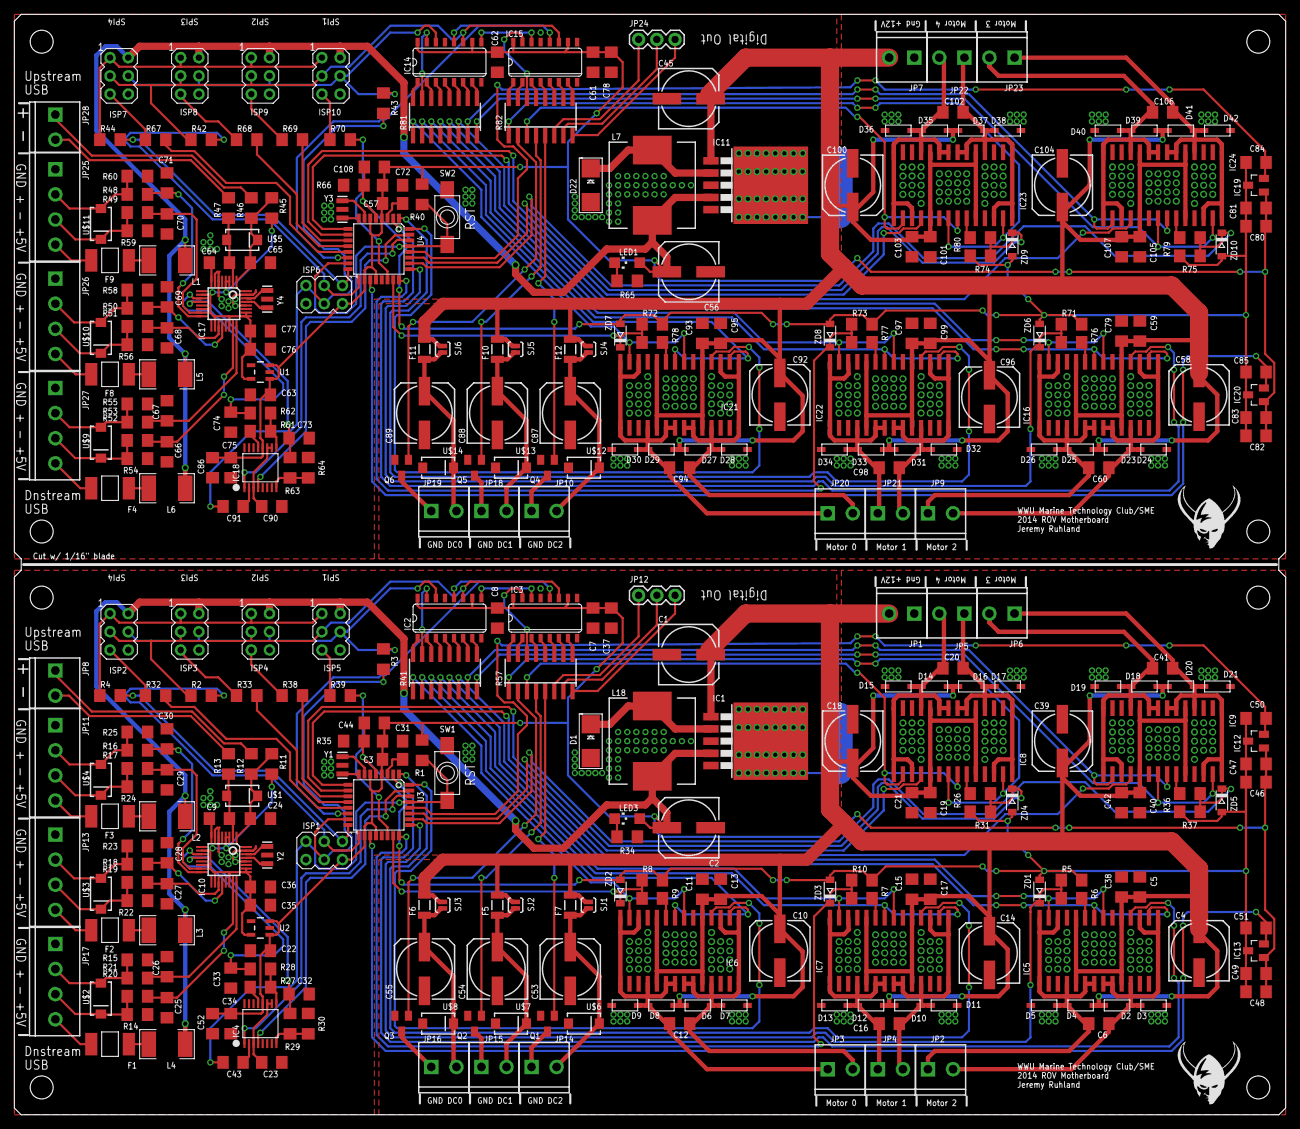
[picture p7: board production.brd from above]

Board: 2 copper layers, 177.2 x 153.4 mm, 362 parts (0 on the bottom side), 246 nets.

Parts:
C1, C2, C45, C53, C54, C55, C56, C87, C88, C89: 1000uF; 153CLV-0807
C3, C5, C7, C8, C11, C15, C19, C23, C34, C36, C40, C43, C44, C47, C49, C50, C51, C57, C59, C61, C62, C75, C77, C81, C83, C84, C85, C90, C91, C93, C97, C101, C105, C108: 0.1uF; C1206
C4, C10, C14, C18, C39, C58, C92, C96, C100, C104: 500uF; 153CLV-0807
C6, C12, C16, C20, C41, C60, C94, C98, C102, C106: 1uF; C1206
C9, C24, C25, C26, C27, C28, C29, C30, C32, C33, C64, C65, C66, C67, C68, C69, C70, C71, C73, C74: 47pF; C1206
C13, C17, C21, C22, C31, C35, C37, C38, C42, C46, C48, C52, C63, C72, C76, C78, C79, C80, C82, C86, C95, C99, C103, C107: 4.7uF; C1206
D1, D22: SMADIODE
D2, D3, D4, D5, D6, D7, D8, D9, D10, D11, D12, D13, D14, D15, D16, D17, D18, D19, D20, D21, D23, D24, D25, D26, D27, D28, D29, D30, D31, D32, D33, D34, D35, D36, D37, D38, D39, D40, D41, D42: SOD-123
F1, F2, F3, F4, F8, F9: 500mA; PTC1812L
F5, F6, F7, F10, F11, F12: PTCSMD; PTC-1206
IC1, IC11: LM2576; TO263-5
IC2, IC3, IC14, IC15: 74LS595D; SO16
IC4, IC18: IC_FT230X-SSOP-16; SSOP-16-FTDI
IC5, IC6, IC7, IC8, IC9, IC16, IC21, IC22, IC23, IC24: VN5772AK; SO-28
IC10, IC17: TUSB2046B; LQFP-32
IC12, IC13, IC19, IC20: LM50; SOT23
ISP1, ISP2, ISP3, ISP4, ISP5, ISP6, ISP7, ISP8, ISP9, ISP10: AVRISP-6; AVRISP
JP1, JP2, JP3, JP4, JP5, JP6, JP7, JP8, JP9, JP10, JP14, JP15, JP16, JP18, JP19, JP20, JP21, JP22, JP23, JP28: SCREWTERMINAL-3.5MM-2
JP11, JP13, JP17, JP25, JP26, JP27: SCREWTERMINAL-3.5MM-4
JP12, JP24: 1X03
L1, L2, L3, L4, L5, L6: INDUCTOR-1206
L7, L18: 100uH; CDRH125
LED1, LED3: CHIPLED_1206
Q1, Q2, Q3, Q4, Q5, Q6: SOT23
R1, R2, R3, R4, R32, R33, R38, R39, R40, R42, R43, R44, R67, R68, R69, R70: 10k; R1206
R5, R8, R10, R31, R37, R71, R72, R73, R74, R75: 2k; R1206
R6, R7, R9, R26, R36, R76, R77, R78, R79, R80: 70; R1206
R11, R45: 1.5k; R1206
R12, R13, R16, R17, R18, R19, R20, R21, R28, R29, R46, R47, R48, R49, R50, R51, R52, R53, R62, R63: 27; R1206
R14, R15, R22, R23, R24, R25, R27, R30, R54, R55, R56, R58, R59, R60, R61, R64: 15k; R1206
R34, R65: 500; R1206
R35, R66: 0; R1206
R41, R57, R81, R82: 10k; SO16
SJ1, SJ2, SJ3, SJ4, SJ5, SJ6: JMP; SJ_2S-NO
SW1, SW2: FSMSM
U1, U2: NCP4625; SOT23-5
U3, U4: ATMEGA168; TQFP32-08
U$1, U$2, U$3, U$4, U$5, U$6, U$7, U$8, U$9, U$10, U$11, U$12, U$13, U$14: TVS; SMA-DIODE
Y1, Y3: 16Mhz; RESONATOR-SMD
Y2, Y4: 6MHz; RESONATOR-SMD
ZD1, ZD2, ZD3, ZD4, ZD5, ZD6, ZD7, ZD8, ZD9, ZD10: 5V; SOD-123

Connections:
0HA: IC6.2, IC6.8, R41.2
0HA1: IC21.2, IC21.8, R81.2
0HB: IC6.7, IC6.13, R41.1
0HB1: IC21.7, IC21.13, R81.1
0SENSE: R8.1, R9.1, U3.23, ZD2.C
0SENSE1: R72.1, R78.1, U4.23, ZD7.C
0STAT: IC6.4, U3.32
0STAT1: IC21.4, U4.32
1HA: IC7.2, IC7.8, R41.3
1HA1: IC22.2, IC22.8, R81.3
1HB: IC7.7, IC7.13, R41.4
1HB1: IC22.7, IC22.13, R81.4
1SENSE: R7.1, R10.1, U3.24, ZD3.C
1SENSE1: R73.1, R77.1, U4.24, ZD8.C
1STAT: IC7.4, U3.1
1STAT1: IC22.4, U4.1
2HA: IC5.2, IC5.8, R41.5
2HA1: IC16.2, IC16.8, R81.5
2HB: IC5.7, IC5.13, R41.6
2HB1: IC16.7, IC16.13, R81.6
2SENSE: R5.1, R6.1, U3.25, ZD1.C
2SENSE1: R71.1, R76.1, U4.25, ZD6.C
2STAT: IC5.4, U3.2
2STAT1: IC16.4, U4.2
3.3V: C35.1, C36.1, IC10.3, IC10.4, IC10.10, IC10.14, IC10.18, IC10.22, IC10.25, IC10.26, R11.2, U2.5
3.3V1: C76.1, C77.1, IC17.3, IC17.4, IC17.10, IC17.14, IC17.18, IC17.22, IC17.25, IC17.26, R45.2, U1.5
3HA: IC9.2, IC9.8, R41.7
3HA1: IC24.2, IC24.8, R81.7
3HB: IC9.7, IC9.13, R41.8
3HB1: IC24.7, IC24.13, R81.8
3SENSE: R36.1, R37.1, U3.26, ZD5.C
3SENSE1: R75.1, R79.1, U4.26, ZD10.C
3STAT: IC9.4, U3.9
3STAT1: IC24.4, U4.9
4HA: IC8.2, IC8.8, R57.3
4HA1: IC23.2, IC23.8, R82.3
4HB: IC8.7, IC8.13, R57.1
4HB1: IC23.7, IC23.13, R82.1
4SENSE: R26.1, R31.1, U3.27, ZD4.C
4SENSE1: R74.1, R80.1, U4.27, ZD9.C
4STAT: IC8.4, U3.10
4STAT1: IC23.4, U4.10
!EN1: R39.2, U3.22
!EN2: R38.2, U3.11
!EN3: R33.2, U3.12
!EN4: R32.2, U3.13
!EN5: R67.2, U4.13
!EN6: R68.2, U4.12
!EN7: R70.2, U4.22
!EN8: R69.2, U4.11
!RST: C43.1, ISP1.5, R1.1, SW1.B, U3.29
!RST1: C91.1, ISP6.5, R40.1, SW2.B, U4.29
+5V: C2.+, C3.1, C7.1, C8.1, C22.1, C31.1, C34.1, C37.1, C44.1, C46.1, C47.1, C48.1, C49.1, C52.1, IC1.4, IC2.10, IC2.16, IC3.10, IC3.16, IC4.12, IC12.1, IC13.1, ISP1.2, ISP2.2, ISP3.2, ISP4.2, ISP5.2, L2.P$1, L3.P$1, L4.P$1, L18.2, LED3.A, R1.2, U2.1, U2.3, U3.4, U3.6, U3.18, U3.20
+5V1: C56.+, C57.1, C61.1, C62.1, C63.1, C72.1, C75.1, C78.1, C80.1, C81.1, C82.1, C83.1, C86.1, C108.1, IC11.4, IC14.10, IC14.16, IC15.10, IC15.16, IC18.12, IC19.1, IC20.1, ISP6.2, ISP7.2, ISP8.2, ISP9.2, ISP10.2, L1.P$1, L5.P$1, L6.P$1, L7.2, LED1.A, R40.2, U1.1, U1.3, U4.4, U4.6, U4.18, U4.20
+12V: C1.+, C4.+, C5.1, C10.+, C11.1, C13.1, C14.+, C15.1, C17.1, C18.+, C19.1, C21.1, C38.1, C39.+, C40.1, C42.1, D2.C, D4.C, D6.C, D8.C, D10.C, D12.C, D14.C, D16.C, D18.C, D20.C, F5.2, F6.2, F7.2, IC1.1, IC5.5, IC5.10, IC5.19, IC5.24, IC6.5, IC6.10, IC6.19, IC6.24, IC7.5, IC7.10, IC7.19, IC7.24, IC8.5, IC8.10, IC8.19, IC8.24, IC9.5, IC9.10, IC9.19, IC9.24, JP1.2, SJ1.2, SJ2.2, SJ3.2
+12V1: C45.+, C58.+, C59.1, C79.1, C92.+, C93.1, C95.1, C96.+, C97.1, C99.1, C100.+, C101.1, C103.1, C104.+, C105.1, C107.1, D23.C, D25.C, D27.C, D29.C, D31.C, D33.C, D35.C, D37.C, D39.C, D41.C, F10.2, F11.2, F12.2, IC11.1, IC16.5, IC16.10, IC16.19, IC16.24, IC21.5, IC21.10, IC21.19, IC21.24, IC22.5, IC22.10, IC22.19, IC22.24, IC23.5, IC23.10, IC23.19, IC23.24, IC24.5, IC24.10, IC24.19, IC24.24, JP7.2, SJ4.2, SJ5.2, SJ6.2
AGND: C44.2, C46.2, C47.2, C48.2, C49.2, C50.2, C51.2, IC12.3, IC13.3, R5.2, R8.2, R10.2, R31.2, R35.1, R37.2, U3.5, ZD1.A, ZD2.A, ZD3.A, ZD4.A, ZD5.A
AGND1: C80.2, C81.2, C82.2, C83.2, C84.2, C85.2, C108.2, IC19.3, IC20.3, R66.1, R71.2, R72.2, R73.2, R74.2, R75.2, U4.5, ZD6.A, ZD7.A, ZD8.A, ZD9.A, ZD10.A
D1+: C32.1, IC10.12, R29.1
D1+1: C73.1, IC17.12, R63.1
D1-: C33.1, IC10.11, R28.1
D1-1: C74.1, IC17.11, R62.1
GND: C1.-, C2.-, C3.2, C4.-, C5.2, C7.2, C8.2, C9.2, C10.-, C11.2, C13.2, C14.-, C15.2, C17.2, C18.-, C19.2, C21.2, C22.2, C23.2, C24.2, C25.2, C26.2, C27.2, C28.2, C29.2, C30.2, C31.2, C32.2, C33.2, C34.2, C35.2, C36.2, C37.2, C38.2, C39.-, C40.2, C42.2, C52.2, C53.-, C54.-, C55.-, D1.A, D3.A, D5.A, D7.A, D9.A, D11.A, D13.A, D15.A, D17.A, D19.A, D21.A, IC1.3, IC1.5, IC1.6, IC2.8, IC2.13, IC3.8, IC3.13, IC4.5, IC4.13, IC5.6, IC5.16, IC5.17, IC5.26, IC5.27, IC6.6, IC6.16, IC6.17, IC6.26, IC6.27, IC7.6, IC7.16, IC7.17, IC7.26, IC7.27, IC8.6, IC8.16, IC8.17, IC8.26, IC8.27, IC9.6, IC9.16, IC9.17, IC9.26, IC9.27, IC10.6, IC10.7, IC10.8, IC10.27, IC10.28, IC10.31, ISP1.6, ISP2.6, ISP3.6, ISP4.6, ISP5.6, JP1.1, JP11.1, JP13.1, JP17.1, Q1.2, Q2.2, Q3.2, R14.2, R15.2, R22.2, R23.2, R24.2, R25.2, R27.1, R30.1, R34.2, R35.2, SW1.A, U2.2, U3.3, U3.21, U$6.A, U$7.A, U$8.A, Y1.2, Y2.2
GND1: C45.-, C56.-, C57.2, C58.-, C59.2, C61.2, C62.2, C63.2, C64.2, C65.2, C66.2, C67.2, C68.2, C69.2, C70.2, C71.2, C72.2, C73.2, C74.2, C75.2, C76.2, C77.2, C78.2, C79.2, C86.2, C87.-, C88.-, C89.-, C90.2, C92.-, C93.2, C95.2, C96.-, C97.2, C99.2, C100.-, C101.2, C103.2, C104.-, C105.2, C107.2, D22.A, D24.A, D26.A, D28.A, D30.A, D32.A, D34.A, D36.A, D38.A, D40.A, D42.A, IC11.3, IC11.5, IC11.6, IC14.8, IC14.13, IC15.8, IC15.13, IC16.6, IC16.16, IC16.17, IC16.26, IC16.27, IC17.6, IC17.7, IC17.8, IC17.27, IC17.28, IC17.31, IC18.5, IC18.13, IC21.6, IC21.16, IC21.17, IC21.26, IC21.27, IC22.6, IC22.16, IC22.17, IC22.26, IC22.27, IC23.6, IC23.16, IC23.17, IC23.26, IC23.27, IC24.6, IC24.16, IC24.17, IC24.26, IC24.27, ISP6.6, ISP7.6, ISP8.6, ISP9.6, ISP10.6, JP7.1, JP25.1, JP26.1, JP27.1, Q4.2, Q5.2, Q6.2, R54.2, R55.2, R56.2, R58.2, R59.2, R60.2, R61.1, R64.1, R65.2, R66.2, SW2.A, U1.2, U4.3, U4.21, U$12.A, U$13.A, U$14.A, Y3.2, Y4.2
ISP-MISO: ISP1.1, R4.2, U3.16
ISP-MISO1: ISP6.1, R44.2, U4.16
ISP-MOSI: ISP1.4, R3.2, U3.15
ISP-MOSI1: ISP6.4, R43.2, U4.15
ISP-SCK: ISP1.3, R2.2, U3.17
ISP-SCK1: ISP6.3, R42.2, U4.17
LATCH: IC2.12, IC3.12, U3.14
LATCH1: IC14.12, IC15.12, U4.14
MISO: ISP2.1, ISP3.1, ISP4.1, ISP5.1, R4.1
MISO1: ISP7.1, ISP8.1, ISP9.1, ISP10.1, R44.1
MOSI: IC2.14, ISP2.4, ISP3.4, ISP4.4, ISP5.4, R3.1
MOSI1: IC14.14, ISP7.4, ISP8.4, ISP9.4, ISP10.4, R43.1
unnamed: D1.C, IC1.2, L18.1
unnamed: U3.8, Y1.3
unnamed: C12.2, D8.A, D9.C, IC6.12, IC6.14, IC6.15, IC6.18, IC6.20, IC6.21, JP3.1
unnamed: U3.7, Y1.1
unnamed: C12.1, D6.A, D7.C, IC6.1, IC6.3, IC6.22, IC6.23, IC6.25, IC6.28, JP3.2
unnamed: IC2.9, IC3.14
unnamed: C9.1, IC10.2, R13.1, U$1.A
unnamed: C16.2, D12.A, D13.C, IC7.12, IC7.14, IC7.15, IC7.18, IC7.20, IC7.21, JP4.1
unnamed: C16.1, D10.A, D11.C, IC7.1, IC7.3, IC7.22, IC7.23, IC7.25, IC7.28, JP4.2
unnamed: C20.2, D16.A, D17.C, IC8.12, IC8.14, IC8.15, IC8.18, IC8.20, IC8.21, JP5.1
unnamed: C20.1, D14.A, D15.C, IC8.1, IC8.3, IC8.22, IC8.23, IC8.25, IC8.28, JP5.2
unnamed: C41.2, D20.A, D21.C, IC9.12, IC9.14, IC9.15, IC9.18, IC9.20, IC9.21, JP6.1
unnamed: C6.2, D4.A, D5.C, IC5.12, IC5.14, IC5.15, IC5.18, IC5.20, IC5.21, JP2.1
unnamed: C41.1, D18.A, D19.C, IC9.1, IC9.3, IC9.22, IC9.23, IC9.25, IC9.28, JP6.2
unnamed: IC3.7, R57.9
unnamed: C43.2, IC4.2
unnamed: IC3.6, R57.10
unnamed: IC3.5, R57.11
unnamed: C24.1, IC10.1, R11.1, R12.1, U$1.C
unnamed: D22.C, IC11.2, L7.1
unnamed: JP17.2, R15.1, R21.1, U$2.A
unnamed: IC10.30, Y2.3
unnamed: IC10.29, Y2.1
unnamed: JP17.3, R14.1, R20.1, U$2.C
unnamed: JP13.3, R19.1, R22.1, U$3.C
unnamed: C30.1, IC10.16, R16.2
unnamed: C29.1, IC10.15, R17.2
unnamed: C28.1, IC10.20, R18.2
unnamed: C27.1, IC10.19, R19.2
unnamed: C25.1, IC10.23, R20.2
unnamed: C26.1, IC10.24, R21.2
unnamed: JP13.2, R18.1, R23.1, U$3.A
unnamed: JP11.3, R17.1, R24.1, U$4.C
unnamed: JP11.2, R16.1, R25.1, U$4.A
unnamed: F1.2, JP17.4
unnamed: F2.2, JP13.4
unnamed: F3.2, JP11.4
unnamed: C23.1, IC4.3, IC4.10, IC4.11
unnamed: IC4.9, R27.2, R28.2
unnamed: IC4.8, R29.2, R30.2
unnamed: F3.1, L2.P$2
unnamed: F2.1, L3.P$2
unnamed: JP14.1, Q1.3
unnamed: JP8.1, R12.2
unnamed: JP8.2, R13.2
unnamed: LED3.C, R34.1
unnamed: JP15.1, Q2.3
unnamed: JP16.1, Q3.3
unnamed: F1.1, L4.P$2
unnamed: C55.+, F6.1, JP16.2, SJ3.1, U$8.C
unnamed: ISP2.5, R32.1
unnamed: ISP3.5, R33.1
unnamed: ISP4.5, R38.1
unnamed: C54.+, F5.1, JP15.2, SJ2.1, U$7.C
unnamed: C53.+, F7.1, JP14.2, SJ1.1, U$6.C
unnamed: IC3.4, R57.12
unnamed: IC14.9, IC15.14
unnamed: ISP5.5, R39.1
unnamed: C6.1, D2.A, D3.C, IC5.1, IC5.3, IC5.22, IC5.23, IC5.25, IC5.28, JP2.2
unnamed: IC3.3, R57.13
unnamed: IC3.2, R57.15
unnamed: IC3.1, R57.16
unnamed: IC3.15, R57.14
unnamed: IC2.7, R41.9
unnamed: IC2.6, R41.10
unnamed: IC2.5, R41.11
unnamed: IC2.4, R41.12
unnamed: IC2.3, R41.13
unnamed: IC2.2, R41.14
unnamed: IC2.1, R41.16
unnamed: IC2.15, R41.15
unnamed: C60.2, D25.A, D26.C, IC16.12, IC16.14, IC16.15, IC16.18, IC16.20, IC16.21, JP9.1
unnamed: C64.1, IC17.2, R47.1, U$5.A
unnamed: C65.1, IC17.1, R45.1, R46.1, U$5.C
unnamed: IC17.30, Y4.3
unnamed: IC5.9, R6.2
unnamed: IC7.9, R7.2
unnamed: IC6.9, R9.2
unnamed: IC9.9, R36.2
unnamed: IC8.9, R26.2
unnamed: IC17.29, Y4.1
unnamed: C71.1, IC17.16, R48.2
unnamed: C70.1, IC17.15, R49.2
unnamed: C69.1, IC17.20, R50.2
unnamed: C68.1, IC17.19, R51.2
unnamed: C66.1, IC17.23, R52.2
unnamed: C67.1, IC17.24, R53.2
unnamed: JP27.2, R53.1, R55.1, U$9.A
unnamed: JP27.3, R52.1, R54.1, U$9.C
unnamed: JP26.3, R51.1, R56.1, U$10.C
unnamed: JP26.2, R50.1, R58.1, U$10.A
unnamed: JP25.3, R49.1, R59.1, U$11.C
unnamed: JP25.2, R48.1, R60.1, U$11.A
unnamed: F4.2, JP27.4
unnamed: F8.2, JP26.4
unnamed: F9.2, JP25.4
unnamed: JP28.1, R46.2
unnamed: JP28.2, R47.2
unnamed: U4.8, Y3.3
unnamed: U4.7, Y3.1
unnamed: C90.1, IC18.3, IC18.10, IC18.11
unnamed: IC18.9, R61.2, R62.2
unnamed: IC18.8, R63.2, R64.2
unnamed: F9.1, L1.P$2
unnamed: F8.1, L5.P$2
unnamed: F4.1, L6.P$2
unnamed: JP10.1, Q4.3
unnamed: JP18.1, Q5.3
unnamed: JP19.1, Q6.3
unnamed: LED1.C, R65.1
unnamed: ISP7.5, R67.1
unnamed: ISP8.5, R68.1
unnamed: ISP9.5, R69.1
unnamed: ISP10.5, R70.1
unnamed: C89.+, F11.1, JP19.2, SJ6.1, U$14.C
unnamed: C88.+, F10.1, JP18.2, SJ5.1, U$13.C
unnamed: C87.+, F12.1, JP10.2, SJ4.1, U$12.C
unnamed: C91.2, IC18.2
unnamed: C60.1, D23.A, D24.C, IC16.1, IC16.3, IC16.22, IC16.23, IC16.25, IC16.28, JP9.2
unnamed: C94.2, D29.A, D30.C, IC21.12, IC21.14, IC21.15, IC21.18, IC21.20, IC21.21, JP20.1
unnamed: C94.1, D27.A, D28.C, IC21.1, IC21.3, IC21.22, IC21.23, IC21.25, IC21.28, JP20.2
unnamed: C98.2, D33.A, D34.C, IC22.12, IC22.14, IC22.15, IC22.18, IC22.20, IC22.21, JP21.1
unnamed: C98.1, D31.A, D32.C, IC22.1, IC22.3, IC22.22, IC22.23, IC22.25, IC22.28, JP21.2
unnamed: C102.2, D37.A, D38.C, IC23.12, IC23.14, IC23.15, IC23.18, IC23.20, IC23.21, JP22.1
unnamed: C102.1, D35.A, D36.C, IC23.1, IC23.3, IC23.22, IC23.23, IC23.25, IC23.28, JP22.2
unnamed: C106.2, D41.A, D42.C, IC24.12, IC24.14, IC24.15, IC24.18, IC24.20, IC24.21, JP23.1
unnamed: C106.1, D39.A, D40.C, IC24.1, IC24.3, IC24.22, IC24.23, IC24.25, IC24.28, JP23.2
unnamed: IC15.7, R82.9
unnamed: IC15.6, R82.10
unnamed: IC15.5, R82.11
unnamed: IC15.4, R82.12
unnamed: IC15.3, R82.13
unnamed: IC15.2, R82.15
unnamed: IC15.1, R82.16
unnamed: IC15.15, R82.14
unnamed: IC14.7, R81.9
unnamed: IC14.6, R81.10
unnamed: IC14.5, R81.11
unnamed: IC14.4, R81.12
unnamed: IC14.3, R81.13
unnamed: IC14.2, R81.14
unnamed: IC14.1, R81.16
unnamed: IC14.15, R81.15
unnamed: IC16.9, R76.2
unnamed: IC22.9, R77.2
unnamed: IC21.9, R78.2
unnamed: IC24.9, R79.2
unnamed: IC23.9, R80.2
RXD: IC4.1, U3.30
RXD1: IC18.1, U4.30
SCK: IC2.11, IC3.11, ISP2.3, ISP3.3, ISP4.3, ISP5.3, R2.1
SCK1: IC14.11, IC15.11, ISP7.3, ISP8.3, ISP9.3, ISP10.3, R42.1
SW0: Q3.1, R57.2
SW1: Q2.1, R57.4
SW2: Q1.1, R57.5
SW3: JP12.1, R57.6
SW4: JP12.2, R57.7
SW5: JP12.3, R57.8
SW6: JP24.1, R82.6
SW7: Q4.1, R82.5
SW8: Q5.1, R82.4
SW9: Q6.1, R82.2
SW10: JP24.3, R82.8
SW11: JP24.2, R82.7
TEMP0: C50.1, IC12.2, U3.28
TEMP1: C51.1, IC13.2, U3.19
TEMP2: C84.1, IC19.2, U4.28
TEMP3: C85.1, IC20.2, U4.19
TXD: IC4.4, U3.31
TXD1: IC18.4, U4.31

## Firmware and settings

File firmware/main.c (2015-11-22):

/*******************************************************************************
* ROV Waterside firmware                                                       *
* 2014 WWU Marine Technology Club                                              *
* http://wwumarinetech.org/winter2014/Software/ROVWaterside                    *
* Jeremy Ruhland                                                               *
*                                                                              *
*******************************************************************************/

#include "includes.h"

// Function prototypes
void initGpio(void);
void runCommand(void);
void updateShift(void);
void sendTemps(void);
void sendCurrents(void);
void sendMotorStatus(void);
void allStop(void);

#ifdef DEAD_RECON_DEMO
void deadReconDemo(void);
#endif

// Global variables
volatile uint8_t ReceivedCommand; // Buffer for received command
volatile ShiftRegister16Bit ShiftOut; // Buffer for shift register
volatile uint16_t AnalogValues[8]; // Buffer for ADC results

int main(void) {
    // Initialize all functions
    initGpio();

    spiInit();
    updateShift(); // Zero shift registers

    uartInit();
    adcInit();

    //sei();

    #ifdef DEAD_RECON_DEMO
    deadReconDemo();
    for (;;) {}
    #else

    // Main control loop
    for(;;) {
        ReceivedCommand = uartRx(); // Check buffer for waiting command
        runCommand(); // Parse and run command
    }
    #endif
}

void initGpio(void) {
    // Set all chip select lines high to disable peripherals on startup
    PORTD |= (1<<PD7);
    DDRD |= ((1<<PD1) | (1<<PD7));

    PORTC |= (1<<PC5);
    DDRC |= (1<<PC5);

    PORTB |= ((0<<PB0) | (1<<PB1)); // Set PB0 back to output after testing
    DDRB |= ((0<<PB0) | (1<<PB1) | (1<<PB2) | (1<<PB3) | (1<<PB5)); // Set PB0 back to output after testing
}

void runCommand(void) {
    static uint8_t oldCommand = 0x00;

    // Only run if new command has been received
    if (oldCommand != ReceivedCommand) {
        oldCommand = ReceivedCommand;
        ReceivedCommand = 0x00; // Reset received command to null

        // Parse and execute received commands
        switch (oldCommand) {
           #ifdef DIRECTIONAL_CONTROLLS // Directional motor control protocol
            // Forward
            case CASE_FORWARD :
                allStop();

              #ifdef MOTOR0_REVERSE
                ShiftOut.bit.motor0 = BACKWARD;
              #else
                ShiftOut.bit.motor0 = FORWARD;
              #endif

              #ifdef MOTOR1_REVERSE
                ShiftOut.bit.motor1 = BACKWARD;
              #else
                ShiftOut.bit.motor1 = FORWARD;
              #endif

                updateShift();

                uartTxByte(ACK); // ACK after command
                break;

            // Backward
            case CASE_BACKWARD :
                allStop();

              #ifdef MOTOR0_REVERSE
                ShiftOut.bit.motor0 = FORWARD;
              #else
                ShiftOut.bit.motor0 = BACKWARD;
              #endif

              #ifdef MOTOR1_REVERSE
                ShiftOut.bit.motor1 = FORWARD;
              #else
                ShiftOut.bit.motor1 = BACKWARD;
              #endif

                updateShift();

                uartTxByte(ACK); // ACK after command
                break;

            // Left
            case CASE_LEFT :
                allStop();

              #ifdef MOTOR4_REVERSE
                ShiftOut.bit.motor4 = BACKWARD;
              #else
                ShiftOut.bit.motor4 = FORWARD;
              #endif

                updateShift();

                uartTxByte(ACK); // ACK after command
                break;

            // Right
            case CASE_RIGHT :
                allStop();

              #ifdef MOTOR4_REVERSE
                ShiftOut.bit.motor4 = FORWARD;
              #else
                ShiftOut.bit.motor4 = BACKWARD;
              #endif

                updateShift();

                uartTxByte(ACK); // ACK after command
                break;

            // Up
            case CASE_UP :
                allStop();

              #ifdef MOTOR2_REVERSE
                ShiftOut.bit.motor2 = BACKWARD;
              #else
                ShiftOut.bit.motor2 = FORWARD;
              #endif

              #ifdef MOTOR3_REVERSE
                ShiftOut.bit.motor3 = BACKWARD;
              #else
                ShiftOut.bit.motor3 = FORWARD;
              #endif

                updateShift();

                uartTxByte(ACK); // ACK after command
                break;

            // Down
            case CASE_DOWN :
                allStop();

              #ifdef MOTOR2_REVERSE
                ShiftOut.bit.motor2 = FORWARD;
              #else
                ShiftOut.bit.motor2 = BACKWARD;
              #endif

              #ifdef MOTOR3_REVERSE
                ShiftOut.bit.motor3 = FORWARD;
              #else
                ShiftOut.bit.motor3 = BACKWARD;
              #endif

                updateShift();

                uartTxByte(ACK); // ACK after command
                break;

            // Clockwise
            case CASE_CLOCKWISE :
                allStop();

              #ifdef MOTOR0_REVERSE
                ShiftOut.bit.motor0 = BACKWARD;
              #else
                ShiftOut.bit.motor0 = FORWARD;
              #endif

              #ifdef MOTOR1_REVERSE
                ShiftOut.bit.motor1 = FORWARD;
              #else
                ShiftOut.bit.motor1 = BACKWARD;
              #endif

                updateShift();

                uartTxByte(ACK); // ACK after command
                break;

            // Anticlockwise
            case CASE_ANTICLOCKWISE :
                allStop();

              #ifdef MOTOR0_REVERSE
                ShiftOut.bit.motor0 = FORWARD;
              #else
                ShiftOut.bit.motor0 = BACKWARD;
              #endif

              #ifdef MOTOR1_REVERSE
                ShiftOut.bit.motor1 = BACKWARD;
              #else
                ShiftOut.bit.motor1 = FORWARD;
              #endif

                updateShift();

                uartTxByte(ACK); // ACK after command
                break;

            // All Stop
            case CASE_ALL_STOP :
                allStop();

                uartTxByte(ACK); // ACK after command
                break;

           #else // Individual motor control protocol

            // Motor 0, stop
            case CASE_MOTOR_0_STOP :
                ShiftOut.bit.motor0 = OFF;
                updateShift();

                uartTxByte(ACK); // ACK after command
                break;

            // Motor 0, forward
            case CASE_MOTOR_0_FORWARD :
              #ifdef MOTOR0_REVERSE
                ShiftOut.bit.motor0 = BACKWARD;
              #else
                ShiftOut.bit.motor0 = FORWARD;
              #endif
                updateShift();

                uartTxByte(ACK); // ACK after command
                break;

            // Motor 0, backward
            case CASE_MOTOR_0_BACKWARD :
              #ifdef MOTOR0_REVERSE
                ShiftOut.bit.motor0 = FORWARD;
              #else
                ShiftOut.bit.motor0 = BACKWARD;
              #endif
                updateShift();

                uartTxByte(ACK); // ACK after command
                break;

            // Motor 1, stop
            case CASE_MOTOR_1_STOP :
                ShiftOut.bit.motor1 = OFF;
                updateShift();

                uartTxByte(ACK); // ACK after command
                break;

            // Motor 1, forward
            case CASE_MOTOR_1_FORWARD :
              #ifdef MOTOR1_REVERSE
                ShiftOut.bit.motor1 = BACKWARD;
              #else
                ShiftOut.bit.motor1 = FORWARD;
              #endif
                updateShift();

                uartTxByte(ACK); // ACK after command
                break;

            // Motor 1, backward
            case CASE_MOTOR_1_BACKWARD :
              #ifdef MOTOR1_REVERSE
                ShiftOut.bit.motor1 = FORWARD;
              #else
                ShiftOut.bit.motor1 = BACKWARD;
              #endif
                updateShift();

                uartTxByte(ACK); // ACK after command
                break;

            // Motor 2, stop
            case CASE_MOTOR_2_STOP :
                ShiftOut.bit.motor2 = OFF;
                updateShift();

                uartTxByte(ACK); // ACK after command
                break;

            // Motor 2, forward
            case CASE_MOTOR_2_FORWARD :
              #ifdef MOTOR2_REVERSE
                ShiftOut.bit.motor2 = BACKWARD;
              #else
                ShiftOut.bit.motor2 = FORWARD;
              #endif
                updateShift();

                uartTxByte(ACK); // ACK after command
                break;

            // Motor 2, backward
            case CASE_MOTOR_2_BACKWARD :
              #ifdef MOTOR2_REVERSE
                ShiftOut.bit.motor2 = FORWARD;
              #else
                ShiftOut.bit.motor2 = BACKWARD;
              #endif
                updateShift();

                uartTxByte(ACK); // ACK after command
                break;

            // Motor 3, stop
            case CASE_MOTOR_3_STOP :
                ShiftOut.bit.motor3 = OFF;
                updateShift();

                uartTxByte(ACK); // ACK after command
                break;

            // Motor 3, forward
            case CASE_MOTOR_3_FORWARD :
              #ifdef MOTOR3_REVERSE
                ShiftOut.bit.motor3 = BACKWARD;
              #else
                ShiftOut.bit.motor3 = FORWARD;
              #endif
                updateShift();

                uartTxByte(ACK); // ACK after command
                break;

            // Motor 3, backward
            case CASE_MOTOR_3_BACKWARD :
              #ifdef MOTOR3_REVERSE
                ShiftOut.bit.motor3 = FORWARD;
              #else
                ShiftOut.bit.motor3 = BACKWARD;
              #endif
                updateShift();

                uartTxByte(ACK); // ACK after command
                break;

            // Motor 4, stop
            case CASE_MOTOR_4_STOP :
                ShiftOut.bit.motor4 = OFF;
                updateShift();

                uartTxByte(ACK); // ACK after command
                break;

            // Motor 4, forward
            case CASE_MOTOR_4_FORWARD :
              #ifdef MOTOR4_REVERSE
                ShiftOut.bit.motor4 = BACKWARD;
              #else
                ShiftOut.bit.motor4 = FORWARD;
              #endif
                updateShift();

                uartTxByte(ACK); // ACK after command
                break;

            // Motor 4, backward
            case CASE_MOTOR_4_BACKWARD :
              #ifdef MOTOR4_REVERSE
                ShiftOut.bit.motor4 = FORWARD;
              #else
                ShiftOut.bit.motor4 = BACKWARD;
              #endif
                updateShift();

                uartTxByte(ACK); // ACK after command
                break;

            // All motors stop
            case CASE_ALL_MOTORS_STOP :
                ShiftOut.bit.motor0 = OFF;
                ShiftOut.bit.motor1 = OFF;
                ShiftOut.bit.motor2 = OFF;
                ShiftOut.bit.motor3 = OFF;
                ShiftOut.bit.motor4 = OFF;
                
                updateShift();

                uartTxByte(ACK); // ACK after command
                break;

            // Toggle SW 0
            case CASE_TOGGLE_SW_0 :
                ShiftOut.bit.switch0 = !(ShiftOut.bit.switch0);

                updateShift();

                if (ShiftOut.bit.switch0) {
                    uartTxByte(ACK); // ACK if on
                } else {
                    uartTxWord((uint16_t) NAK); // NAK if off
                }
                break;

            // Toggle SW 1
            case CASE_TOGGLE_SW_1 :
                ShiftOut.bit.switch1 = !(ShiftOut.bit.switch1);

                updateShift();

                if (ShiftOut.bit.switch1) {
                    uartTxByte(ACK); // ACK if on
                } else {
                    uartTxWord((uint16_t) NAK); // NAK if off
                }
                break;

            // Toggle SW 2
            case CASE_TOGGLE_SW_2 :
                ShiftOut.bit.switch2 = !(ShiftOut.bit.switch2);

                updateShift();

                if (ShiftOut.bit.switch2) {
                    uartTxByte(ACK); // ACK if on
                } else {
                    uartTxWord((uint16_t) NAK); // NAK if off
                }
                break;

            // Toggle SW 3
            case CASE_TOGGLE_SW_3 :
                ShiftOut.bit.switch3 = !(ShiftOut.bit.switch3);

                updateShift();

                if (ShiftOut.bit.switch3) {
                    uartTxByte(ACK); // ACK if on
                } else {
                    uartTxWord((uint16_t) NAK); // NAK if off
                }
                break;

            // Toggle SW 4
            case CASE_TOGGLE_SW_4 :
                ShiftOut.bit.switch4 = !(ShiftOut.bit.switch4);

                updateShift();

                if (ShiftOut.bit.switch4) {
                    uartTxByte(ACK); // ACK if on
                } else {
                    uartTxWord((uint16_t) NAK); // NAK if off
                }
                break;

            // Toggle SW 5
            case CASE_TOGGLE_SW_5 :
                ShiftOut.bit.switch5 = !(ShiftOut.bit.switch5);

                updateShift();

                if (ShiftOut.bit.switch5) {
                    uartTxByte(ACK); // ACK if on
                } else {
                    uartTxWord((uint16_t) NAK); // NAK if off
                }
                break;

            // All switches off
            case CASE_ALL_SWITCHES_OFF :
                ShiftOut.bit.switch0 = OFF;
                ShiftOut.bit.switch1 = OFF;
                ShiftOut.bit.switch2 = OFF;
                ShiftOut.bit.switch3 = OFF;
                ShiftOut.bit.switch4 = OFF;
                ShiftOut.bit.switch5 = OFF;

                updateShift();

                uartTxByte(ACK); // ACK after command
                break;

            // Get all motor status
            case CASE_MOTOR_STATUS :
                sendMotorStatus();
                break;

            // Get all temps
            case CASE_TEMPS :
                sendTemps();
                break;

            // Get all motor currents
            case CASE_CURRENTS :
                sendCurrents();
                break;

            // Get water conductivity measurement
            case CASE_CONDUCTIVITY :

                break;

            // Get sonar distance measurement
            case CASE_SONAR_DISTANCE :

                break;

            // Get compass heading
            case CASE_COMPASS :

                break;

            default:
                break;
           #endif
        }

       #ifdef TEXT_DEBUG
        // Debug routine to print human readable state information
        switch (oldCommand) {
            // Motor 0, stop
            case CASE_MOTOR_0_STOP :
                uartTxStrg("\n\rMotor 0 Stop");
                break;

            // Motor 0, forward
            case CASE_MOTOR_0_FORWARD :
                uartTxStrg("\n\rMotor 0 Forward");
                break;

            // Motor 0, backward
            case CASE_MOTOR_0_BACKWARD :
                uartTxStrg("\n\rMotor 0 Backward");
                break;

            // Motor 1, stop
            case CASE_MOTOR_1_STOP :
                uartTxStrg("\n\rMotor 1 Stop");
                break;

            // Motor 1, forward
            case CASE_MOTOR_1_FORWARD :
                uartTxStrg("\n\rMotor 1 Forward");
                break;

            // Motor 1, backward
            case CASE_MOTOR_1_BACKWARD :
                uartTxStrg("\n\rMotor 1 Backward");
                break;

            // Motor 2, stop
            case CASE_MOTOR_2_STOP :
                uartTxStrg("\n\rMotor 2 Stop");
                break;

            // Motor 2, forward
            case CASE_MOTOR_2_FORWARD :
                uartTxStrg("\n\rMotor 2 Forward");
                break;

            // Motor 2, backward
            case CASE_MOTOR_2_BACKWARD:
                uartTxStrg("\n\rMotor 2 Backward");
                break;

            // Motor 3, stop
            case CASE_MOTOR_3_STOP :
                uartTxStrg("\n\rMotor 3 Stop");
                break;

            // Motor 3, forward
            case CASE_MOTOR_3_FORWARD :
                uartTxStrg("\n\rMotor 3 Forward");
                break;

            // Motor 3, backward
            case CASE_MOTOR_3_BACKWARD :
                uartTxStrg("\n\rMotor 3 Backward");
                break;

            // Motor 4, stop
            case CASE_MOTOR_4_STOP :
                uartTxStrg("\n\rMotor 4 Stop");
                break;

            // Motor 4, forward
            case CASE_MOTOR_4_FORWARD :
                uartTxStrg("\n\rMotor 4 Forward");
                break;

            // Motor 4, backward
            case CASE_MOTOR_4_BACKWARD :
                uartTxStrg("\n\rMotor 4 Backward");
                break;

            // All motors stop
            case CASE_ALL_MOTORS_STOP :
                uartTxStrg("\n\rAll Motors Stop");
                break;

            default:
                uartTxStrg("\n\rUnknown Command");
                break;
        }
       #endif
    }
}

void sendMotorStatus(void) {
}

void sendTemps(void) {
    int16_t temp;
    uint8_t i;

    // Convert analog values and send
    for (i = 0; i <= 2; i++) {
        temp = adcFormatTemp(AnalogValues[i+5]);
        uartTxWord(temp);
    }
}

void sendCurrents(void) {
    uint16_t currents[5];
    uint8_t i;

    // Convert analog values to currents array
    for (i = 0; i <= 4; i++) {
        currents[i] = adcFormatVoltage(AnalogValues[i]);
    }

    // Send currents array
    for (i = 0; i <= 4; i++) {
        uartTxWord(currents[i]);
    }
}

void updateShift(void) {
    spiPeripheralSelect(0); // Disable all peripherals

    // Transmit new shift register data
    (void) spiByte((uint8_t) ShiftOut.uart);
    (void) spiByte((uint8_t) (ShiftOut.uart>>8));

    _delay_us(0.025); // Delay 25nS for setup time of shift register

    // Rising edge on latch, delay and drop
    PORTB |= (1<<PB2);
    _delay_us(0.025); // Delay 25nS for setup time of shift register
    PORTB &= ~(1<<PB2);
}

ISR(ADC_vect) {
    static uint8_t adcMux = 0;

    if (adcMux <= 3) { // Motor 0-4
        AnalogValues[adcMux] = adcResult();

        adcMux++;

        ADMUX = ((ADMUX & ~(0x0F)) | adcMux); // Switch to next mux

        // Start new conversion
        ADCSRA |= (1<<ADSC);
    } else if (adcMux == 4) { // Skip EN1
        AnalogValues[adcMux] = adcResult();
    
        adcMux += 2;

        ADMUX = ((ADMUX & ~(0x0F)) | adcMux); // Switch to next mux
        
        // Start new conversion
        ADCSRA |= (1<<ADSC);
    } else if (adcMux <= 7) { // Temp 0-1
        AnalogValues[adcMux-1] = adcResult();

        adcMux++;

        ADMUX = ((ADMUX & ~(0x0F)) | adcMux); // Switch to next mux

        // Start new conversion
        ADCSRA |= (1<<ADSC);
    } else { // Internal Temp
        AnalogValues[adcMux-1] = adcResult();

        adcMux = 0; // Reset cycle

        ADMUX = ((ADMUX & ~(0x0F)) | adcMux); // Switch to next mux

        // Start new conversion
        ADCSRA |= (1<<ADSC);
    }
}

void allStop(void) {
    // Turn off all motors
    ShiftOut.uart = (uint16_t) OFF;
    updateShift();
    
    _delay_ms(1); // Let bridges settle
}

#ifdef DEAD_RECON_DEMO
void deadReconDemo(void) {
#if 0
    // This is uart debug code
    for(;;) {
        uartTxByte('q');

        uartTxStrg("");
        _delay_ms(100);
    }
#endif
#if 0
    // This is spi output code to test speeds
    uint8_t i = 0;

    for (;;) {
        //_delay_ms(1);
        spiPeripheralSelect(4);
        _delay_us(20);
        spiByte(i);
        spiPeripheralSelect(0);
        i++;
        //_delay_us(200);
    }
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

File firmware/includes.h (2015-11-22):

/*******************************************************************************
* Main Includes File                                                           *
*                                                                              *
* Program setting defines:                                                     *
* Uncomments these lines to enable features. If motors run backwards, reverse  *
* them here. If shift register receives data in reverse order, enable          *
* bitfield order reverse mode.                                                 *
* Uncommenting text debug mode will cause the ROV to print serial strings      *
* describing its current state.                                                *
* Uncommenting the dead recon demo will automatically comment out all normal   *
* code and run a predefined demo program.                                      *
*                                                                              *
*******************************************************************************/

#define MOTOR0_REVERSE
#define MOTOR1_REVERSE
// #define MOTOR2_REVERSE
// #define MOTOR3_REVERSE
#define MOTOR4_REVERSE

// #define BITFIELD_ORDER_REVERSE

// #define TEXT_DEBUG

// #define DEAD_RECON_DEMO

#define DIRECTIONAL_CONTROLLS

/*****************************************************************************/

#include <avr/io.h>
#include <util/delay.h>
#include <avr/interrupt.h>

#include "spi.h"
#include "uart.h"
#include "adc.h"

#define ACK      'y'
#define NAK      'n'

#define FORWARD  0x01
#define BACKWARD 0x02
#define ON       0x01
#define OFF      0x00
#define TRUE     0x01
#define FALSE    0x00

#ifdef DIRECTIONAL_CONTROLLS

#define CASE_FORWARD          (uint8_t) 'w'
#define CASE_BACKWARD         (uint8_t) 's'
#define CASE_LEFT             (uint8_t) 'a'
#define CASE_RIGHT            (uint8_t) 'd'
#define CASE_UP               (uint8_t) 'u'
#define CASE_DOWN             (uint8_t) 'j'
#define CASE_CLOCKWISE        (uint8_t) 'e'
#define CASE_ANTICLOCKWISE    (uint8_t) 'q'
#define CASE_ALL_STOP         (uint8_t) ' '

#else

#define CASE_MOTOR_0_STOP     (uint8_t) '`'
#define CASE_MOTOR_0_FORWARD  (uint8_t) '1'
#define CASE_MOTOR_0_BACKWARD (uint8_t) '2'
#define CASE_MOTOR_1_STOP     (uint8_t) '3'
#define CASE_MOTOR_1_FORWARD  (uint8_t) '4'
#define CASE_MOTOR_1_BACKWARD (uint8_t) '5'
#define CASE_MOTOR_2_STOP     (uint8_t) '6'
#define CASE_MOTOR_2_FORWARD  (uint8_t) '7'
#define CASE_MOTOR_2_BACKWARD (uint8_t) '8'
#define CASE_MOTOR_3_STOP     (uint8_t) '9'
#define CASE_MOTOR_3_FORWARD  (uint8_t) '0'
#define CASE_MOTOR_3_BACKWARD (uint8_t) '-'
#define CASE_MOTOR_4_STOP     (uint8_t) '='
#define CASE_MOTOR_4_FORWARD  (uint8_t) 'q'
#define CASE_MOTOR_4_BACKWARD (uint8_t) 'w'
#define CASE_ALL_MOTORS_STOP  (uint8_t) 'e'
#define CASE_TOGGLE_SW_0      (uint8_t) 'r'
#define CASE_TOGGLE_SW_1      (uint8_t) 't'
#define CASE_TOGGLE_SW_2      (uint8_t) 'y'
#define CASE_TOGGLE_SW_3      (uint8_t) 'u'
#define CASE_TOGGLE_SW_4      (uint8_t) 'i'
#define CASE_TOGGLE_SW_5      (uint8_t) 'o'
#define CASE_ALL_SWITCHES_OFF (uint8_t) 'p'
#define CASE_MOTOR_STATUS     (uint8_t) '['
#define CASE_TEMPS            (uint8_t) ']'
#define CASE_CURRENTS         (uint8_t) '\\'
#define CASE_CONDUCTIVITY     (uint8_t) 'a'
#define CASE_SONAR_DISTANCE   (uint8_t) 's'
#define CASE_COMPASS          (uint8_t) 'd'

#endif

#ifdef BITFIELD_ORDER_REVERSE
typedef struct {
    uint8_t motor0  : 2;
    uint8_t motor1  : 2;
    uint8_t motor2  : 2;
    uint8_t motor3  : 2;
    uint8_t motor4  : 2;
    uint8_t switch0 : 1;
    uint8_t switch1 : 1;
    uint8_t switch2 : 1;
    uint8_t switch3 : 1;
    uint8_t switch4 : 1;
    uint8_t switch5 : 1;
} bitfield;
#else
typedef struct {
    uint8_t switch5 : 1;
    uint8_t switch4 : 1;
    uint8_t switch3 : 1;
    uint8_t switch2 : 1;
    uint8_t switch1 : 1;
    uint8_t switch0 : 1;
    uint8_t motor4  : 2;
    uint8_t motor3  : 2;
    uint8_t motor2  : 2;
    uint8_t motor1  : 2;
    uint8_t motor0  : 2;
} bitfield;
#endif

typedef union ShiftRegister16Bit {
    uint16_t uart;
    bitfield bit;
} ShiftRegister16Bit;

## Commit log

2013-11-30 Started prelim motherboard design.
    [motherboard.sch]
2013-12-02 updated mobo sch
    [motherboard.sch]
2013-12-02 replicated h-bridges, added usb chip
    [motherboard.sch]
2013-12-02 usb components
    [motherboard.sch]
2013-12-07 replacing usb enabled uC with two chip solution
    [motherboard.sch]
2013-12-08 added usb/ttl
    [motherboard.sch]
2013-12-09 rearranged some signals, corrected cap values
    [motherboard.sch]
2013-12-09 working on conductivity sensor circuit
    [motherboard.sch]
2013-12-09 reorganized analog sensor
    [motherboard.sch]
2013-12-10 added thermal sensors, external switches
    [motherboard.sch]
2013-12-15 fixed conductivity circuit, connected agnd->gnd
    [motherboard.sch]
2013-12-21 3.3v regulator datasheet added
2013-12-21 validating subcomponents
    [motherboard.sch]
2013-12-24 finished subsystem validatation
    [motherboard.sch]
2013-12-25 updated sch
    [motherboard.sch]
2013-12-29 started pcb with initial measurments
    [motherboard.brd]
2013-12-31 laying out subsystems
    [motherboard.brd]
2014-01-03 added missing reset capacitor
    [motherboard.sch]
2014-01-10 rewired h-bridges to not short out and simplified trace layout
    [motherboard.brd, motherboard.sch]
2014-01-13 added current liminting resistors to shift registers
    [motherboard.brd, motherboard.sch]
2014-01-14 laying out protection diodes
    [motherboard.brd, motherboard.sch]
2014-01-14 added bill of materials
2014-01-15 making BOM
2014-01-15 laying out hbridges
    [motherboard.brd]
2014-01-15 added more bom part numbers
    [bill_of_materials.csv]
2014-01-16 working on BOM
    [bill_of_materials.csv]
2014-01-17 worked on BOM
    [bill_of_materials.csv]
2014-01-17 laying out components
    [motherboard.brd, motherboard.sch]
2014-01-18 changing h bridge layout
    [motherboard.brd, motherboard.sch]
2014-01-19 layed out hbridges, MCU, new fuses
    [bill_of_materials.csv, motherboard.brd, motherboard.sch]
2014-01-21 positioned all but mcu
    [bill_of_materials.csv, motherboard.brd, motherboard.sch]
2014-01-21 putting things into place
    [motherboard.brd]
2014-01-21 layed out control lines to hbridges, fets
    [motherboard.brd, motherboard.sch]
2014-01-22 moved in risers
    [motherboard.brd]
2014-01-22 moved ruler
    [motherboard.brd]
2014-01-26 laying out mcu
    [bill_of_materials.csv, motherboard.brd, motherboard.sch]
2014-01-27 finished initial routing
    [motherboard.brd]
2014-01-27 finished silkscreen
    [motherboard.brd, motherboard.sch]
2014-01-27 added bw footprint image
2014-01-28 corrected and checked BOM
    [bill_of_materials.csv]
2014-01-28 added excell bom list for budget expantion
    [BOM_pricequote.xlsx]
2014-01-29 creating production gerber layout
    [production.brd]
2014-01-29 last changes to motherboard
    [motherboard.brd]
2014-01-29 started correcting CAM errors on motherboard directly
    [motherboard.brd]
2014-01-29 corrected drc errors except overlap under 5v buck
    [motherboard.brd]
2014-01-29 added corrected motherboard to production board
    [production.brd]
2014-01-29 finished production board design
    [production.brd]
2014-01-30 final changes to boards for production
    [motherboard.brd, production.brd]
2014-01-30 tweaks to boards
    [motherboard.brd, production.brd]
2014-01-30 added gerber zip
2014-02-04 working on adc
2014-02-05 adc isr routine
2014-02-10 adc module done
2014-02-10 uart module done
2014-02-10 uart modlue done
2014-02-10 adding in motor control
2014-02-10 reconfigured motor commands
2014-02-11 adding temp and current code
2014-02-11 finished adc
2014-02-11 finished uart
2014-02-11 finish spi
2014-02-11 fixed typedefs causing bugs in main
    [includes.h, main.c]
2014-02-15 fixed errors from unclosed if/else's, fixed warning in uart clockrate define
    [main.c]
2014-02-24 added dead recon mode, debug mode, fixed motor control error, proved system
    [includes.h, main.c, uart.c]
2014-04-23 switched to new programmer
2014-04-23 still working on string tx issue
    [uart.c]
2014-05-07 final define changes to reverse backwards motors
    [includes.h, main.c]
2015-11-22 moved everything to hardware folder
    [BOM_pricequote.xlsx, bill_of_materials.csv, motherboard.brd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]

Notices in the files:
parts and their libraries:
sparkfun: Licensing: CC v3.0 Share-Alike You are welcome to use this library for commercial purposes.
